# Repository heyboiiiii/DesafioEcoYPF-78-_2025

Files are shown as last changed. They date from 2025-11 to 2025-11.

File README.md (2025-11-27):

# PROYECTO YPF

## El proyecto original tenía como objetivo desarrollar la Computadora del Auto completa para el Desafío ECO YPF, incorporando diversos módulos de control y adquisición de datos para asistir al piloto. Dentro del conjunto de la Computadora, el Sistema de Control de Velocidad Crucero representaba solo una de las funcionalidades planificadas.
Sin embargo, durante el proceso surgieron diversos imprevistos que modificaron el alcance del proyecto. El viaje al autódromo, condiciones climáticas de tormenta que impidieron trabajar sobre el vehículo y, finalmente, un choque que dañó la placa principal del auto, imposibilitaron continuar con la integración de la computadora completa. Como consecuencia, se decidió enfocar el proyecto al desarrollo y funcionamiento del sistema de velocidad crucero utilizando una placa experimental.
Esta reestructuración permitió concentrarse en el diseño, programación y prueba del sistema decontrol de velocidad mediante ESP32, GPS y servomotor, con un sistema PID. Aunque no fue posible implementar la computadora entera del vehículo, el repositorio oficial del proyecto incluye el código completo de todos los módulos de la computadora, documentado y accesible.
En este informe se detalla el funcionamiento del sistema de velocidad crucero, su implementación, las pruebas realizadas y los resultados obtenidos en función del ensayo con la placa experimental.

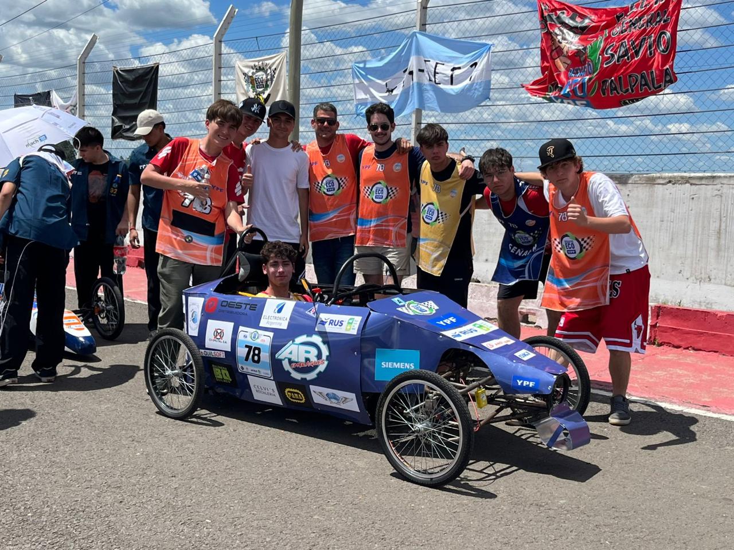
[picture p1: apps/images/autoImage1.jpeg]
FOTO 1 AUTO

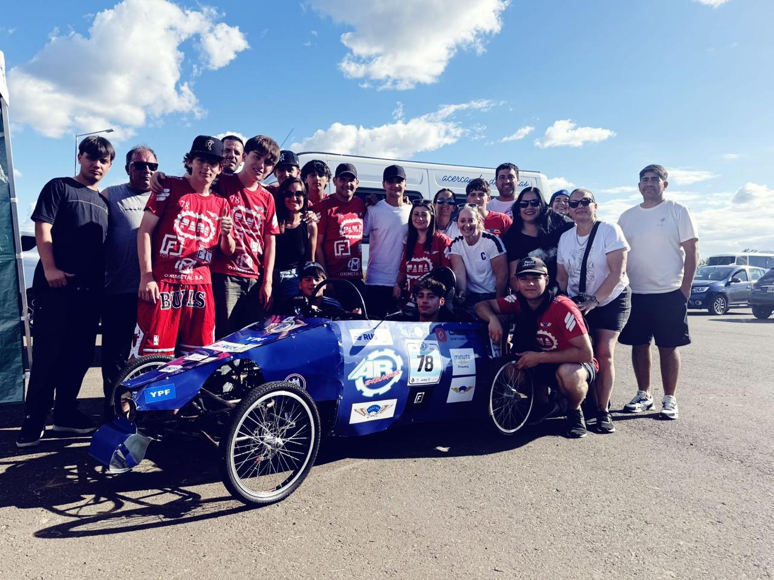
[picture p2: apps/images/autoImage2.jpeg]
FOTO 2 AUTO


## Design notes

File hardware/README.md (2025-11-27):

YPF KICAD DESIGNS

Esquemas y PCB de KICAD para la computadora del auto del "Desafío ECO YPF" y sus submódulos.

Proyecto *AUTO*:
    
    Computadora basada en un ESP32, una pantalla led ILI9844 montada en el volante(SPI), un acelerometro(MPU6050), modulo GPS(NEO6M) y un modulo LORA(XL1278).  

Proyecto *SHIELD_LORA*:
    
    Adaptación del módulo SMT1278 LoRa a un conector de 5 pines (header de 2.54 mm).

Proyecto *ACS_V_placa*:
    
    Aquí es donde los terminales de las baterías se conectan al sensor de corriente ACS712 (30A) y al divisor de voltaje.

    Esta placa se conectará a la placa del Proyecto AUTO mediante 3 cables.

Project_libraries: librerias de simbolos y huellas de los componentes creados para adaptar cada modulo a la placa.

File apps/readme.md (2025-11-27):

# Pagina web 

# Esta se encarga de mostrar al usuario toda la informacion que puede sensar la computadora del auto y la envia a traves de un modulo Lora SMT1278.

# La pagina web es alojada internamente en un servidor montado con LittleFS sobre el esp32 conectado en boxes como receptor.

# Para acceder a esta se debe primero conectar al Access Point generado por el esp32 con las credenciales cargadas y entrar por un navegador a la direccion IP del esp32 por el puerto 80.

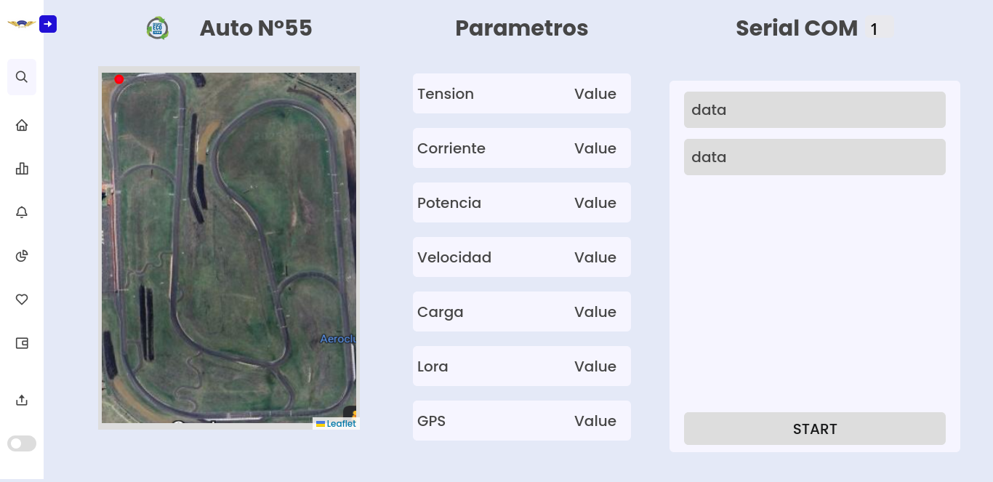
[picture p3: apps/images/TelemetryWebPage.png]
Muestra de la pagina web


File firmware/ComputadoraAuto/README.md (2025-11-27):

Firmware para la Computadora del Auto Desafio ECO YPF 2025

DESCRIPCIÓN DE LIBRERIAS

Libreria del Display (Manejo del display y fuentes de escritura):
    DISPLAY.c/.h & FONTS.c/.h

Libreria LoRa (Transmisor a Boxes)

Libreria GPS (NEO-6MV2)

Libreria Acelerómetro y Servo (MPU6050)

Info enviada por LoRa a Boxes:
latitud
longitud
voltaje
corriente
capacidad restante
velocidad

Display en auto:
    posee 2 windows: 
    1 - velocimetro
    2 - info: voltaje, corriente, capacidad bateria

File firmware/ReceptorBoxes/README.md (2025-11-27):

Receptor de telemetria en boxes(LORA).

1- Se recibira por el modulo SMT1278, la siguiente informacion del automovil:

    Tension y Corriente de baterias.
    Velocidad.
    Posicionamiento(Latitud & Longitud).
    Estado de pulsadores del volante.
    
2- Esta informacion es mostrada atraves de una pagina en un servidor interno montado por el esp32 con littleFS en una red local generada por el modulo WiFi del propio microcontrolador.

*Codigo de pagina web mas a detalle en directorio apps:

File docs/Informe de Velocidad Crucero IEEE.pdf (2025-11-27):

# Velocidad Crucero

Computadoras y Sistemas de Control, 6to 2da Avionica Comision A ´

Della Torre, Joaquin
joaquindellatorre@impatrq.com

Romero Domínguez, Braulio braulioromerodominguez@impatrq.com

Przybylski, Facundo
facundoprzybylski@impatrq.com

Reyes, Joaquin
joaquinreyes@impatrq.com

Pulido, Ignacio
ignaciopulido@impatrq.com

Abstract—Este proyecto desarrolla un Sistema de Control de Velocidad Crucero para el auto del Desafío ECO YPF, implementado con un microcontrolador ESP32 y un servomotor accionado mediante un sistema PID. La velocidad del vehículo se obtiene en tiempo real mediante un modulo GPS NEO-6MV2, cuyos datos ´ son procesados para regular la posicion del servo que opera sobre ´ el pedal que mueve el puno acelerador. Las pruebas realizadas ˜ con una placa experimental demostraron que el sistema mantiene una velocidad estable, responde adecuadamente a variaciones y se puede integrar de manera eficaz y segura al auto.

I. INTRODUCCION´
El proyecto original tenía como objetivo desarrollar la Computadora del Auto completa para el Desafío ECO YPF,
incorporando diversos modulos de control y adquisici ´ | on de ´
datos para asistir al piloto, enfocandose en este entorno de ´ taller en específico al sistema de Velocidad Crucero aunque dentro del conjunto de la Computadora, el Sistema de Control de Velocidad Crucero representaba solo una de las funcionalidades planificadas. Sin embargo, durante el proceso surgieron diversos imprevistos que modificaron el alcance del proyecto.
El viaje al autodromo, condiciones clim ´ | aticas de tormenta ´
que impidieron trabajar sobre el vehículo y, finalmente, un choque que danõ la placa principal del auto y en el que se ´
perdio la placa de volt ´ | ímetro y amperímetro que se encon-
traba junto a las baterías, imposibilitaron continuar con la integracion de la computadora completa. Como consecuencia, ´ se decidio enfocar el proyecto al desarrollo y funcionamiento ´ del sistema de Velocidad Crucero utilizando una placa ex-
perimental. Esta reestructuracion permiti ´ | o concentrarse en el ´
diseno, programaci ˜ | on y prueba del sistema de control de ´
velocidad con una ESP32, un modulo GPS y un servomotor, ´ mediante un sistema PID. Aunque no fue posible implementar la computadora entera del vehículo, el repositorio oficial del
proyecto incluye el codigo completo de todos los m ´ | odulos de ´
la computadora, documentado y accesible. En este informe se detalla el funcionamiento del sistema de velocidad crucero, su implementacion, las pruebas realizadas y los resultados ´ obtenidos en funcion del ensayo con la placa experimental. ´

II. DESCRIPCION´ FUNCIONAL

A. Diagrama en Bloques
A continuacion se observa el diagrama en bloques del ´ sistema.

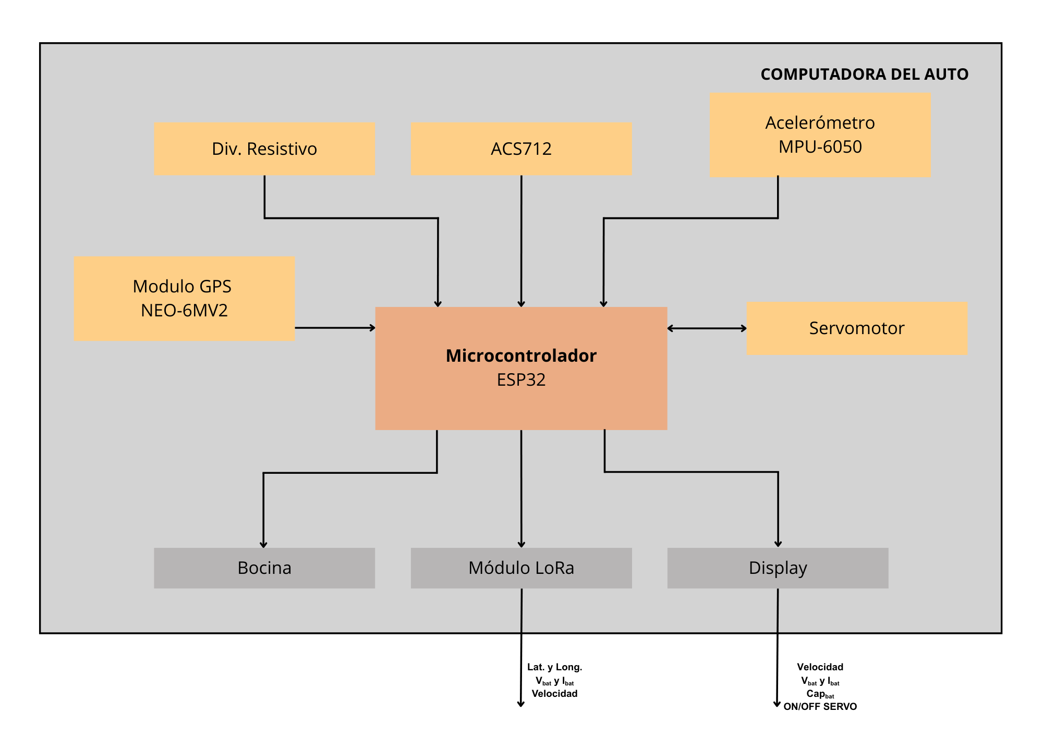
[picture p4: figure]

Fig. 1. Diagrama en bloques.

B. Diagrama de codigo ´

En la Figura 2 puede verse el diagrama de codigo de la ´ velocidad crucero.

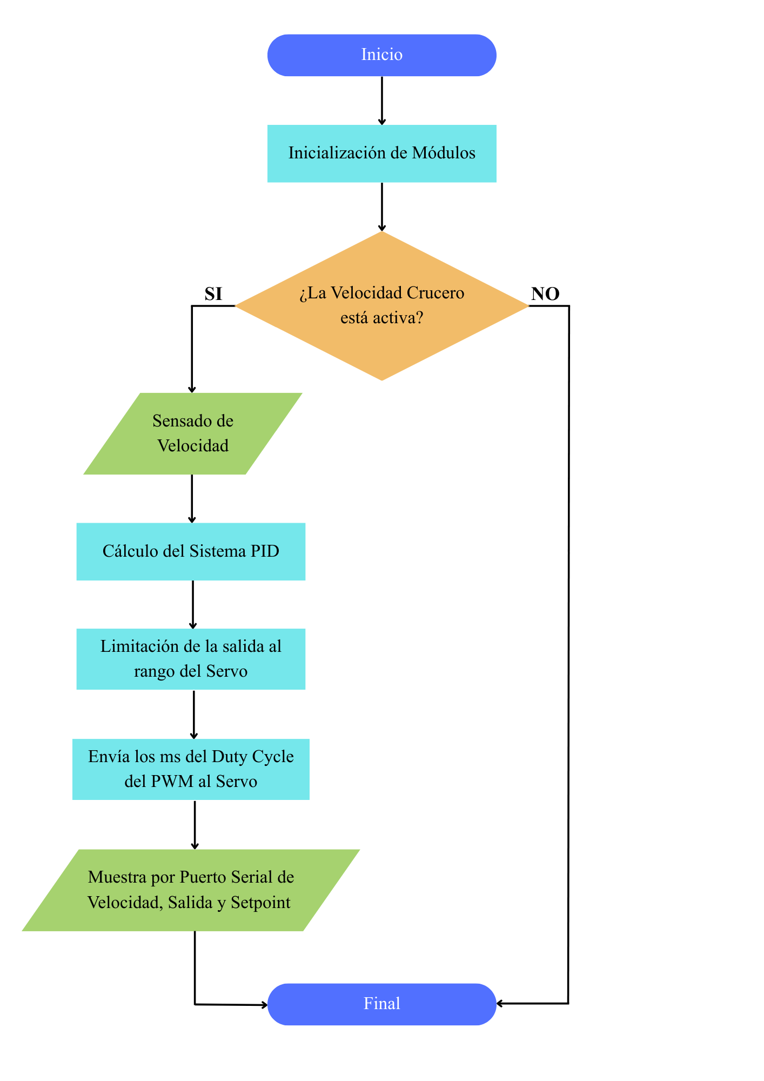
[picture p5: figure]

Fig. 2. Diagrama de codigo. ´

C. Descripcion de circuitos ´
- Modulo GPS: El M ´ | odulo GPS es el encargado de propor- ´
cionar en tiempo real la velocidad a la que se desplaza el auto. En este proyecto utilizamos el modelo NEO-6MV2,
el cual incluye internamente una funcion espec ´ | ífica para
calcular la velocidad a partir de los datos satelitales.
La informacion procesada por el m ´ | odulo es enviada a ´
la ESP32, que se encarga de interpretarla y utilizarla dentro del sistema de control para la implementacion de ´ la velocidad crucero.
- Microcontrolador ESP32: La ESP32 actua como el mi- ´ crocontrolador principal del sistema y es la encargada de procesar los datos de velocidad otorgados por el modulo ´ GPS. Sobre esta se implementa el algoritmo de control PID, que determina como debe actuar el sistema de ´ velocidad crucero. A partir de los calculos del PID, la ´ ESP32 genera la senal PWM necesaria para controlar el ˜ servomotor, ajustando su posicion seg ´ un la velocidad que ´ se desea mantener.
- Servomotor: El servomotor es el actuador principal del sistema de velocidad crucero. Recibe desde la ESP32
una senal PWM que indica el ˜ | angulo exacto al que debe ´
posicionarse. Segun este valor, el servo se mueve y tensa ´
un cable de acero, el cual esta conectado mec ´ | anicamente ´
al pedal del acelerador. Cuando el servomotor tira del cable, el pedal se acciona y, a su vez, este mueve el punõ acelerador, cumpliendo con el reglamento que no autoriza modificar el sistema desde el puno acelerador en adelante. ˜

III. ALCANCE LOGRADO
Logramos desarrollar un sistema de Velocidad Crucero funcional utilizando un microcontrolador ESP32 y un servomotor, cumpliendo el objetivo principal de implementar un sistema de control accesible, aplicable y coherente con el reglamento del Desafío ECO YPF. El sistema es capaz de leer e interpretar en tiempo real la velocidad del auto y ajustar automaticamente el accionamiento del servomotor para ´
mantener la velocidad deseada. En terminos de desempe ´ | no, ˜
su funcion central —accionar el servomotor para acelerar el ´ vehículo de manera estable mientras la Velocidad Crucero está activa— se ejecuta correctamente. Es importante destacar que el alcance final del proyecto, que estuvo influenciado por los diversos imprevistos ocurridos durante las etapas de trabajo, se vio limitado en cuanto a lo que se esperaba. Debido a las circunstancias imprevistas, el sistema debio desarrollarse y ´ probarse sobre una placa experimental independiente, lo que permitio continuar avanzando a pesar de las limitaciones del ´ entorno real.
Aun así, se observaron aspectos positivos, el sistema mostró una respuesta rapida del servomotor, fidelidad en la veloci- ´
dad que brinda el Modulo GPS, y una integraci ´ | on hard- ´
ware–software que demostro ser efectiva. Tambi ´ | en se com- ´
probo que el concepto puede incorporarse al auto sin requerir ´ modificaciones estructurales significativas.
Sin embargo, al tratarse de un ensayo inicial, se identificaron
algunas limitaciones. Sera necesario optimizar la ubicaci ´ | on de ´

la placa, el servomotor y el cableado para evitar interferencias
con el piloto durante la conduccion. Adem ´ | as, en esta prueba ´
la Velocidad Crucero permanecía activa mientras la ESP32 estuviera alimentada, lo cual puede resultar poco practico ´ o incluso riesgoso en situaciones donde el piloto necesite modificar la velocidad sin apagar todo el sistema. En resumen,
el sistema logro cumplir su objetivo funcional y demostr ´ | o un ´
desempeno correcto, aun cuando no se pudo integrar en la ˜ computadora completa del auto.

IV. CONCLUSIONES

El proyecto logro desarrollar un sistema de Velocidad ´ Crucero funcional e innovador para el Desafío ECO YPF, incorporando una característica completamente nueva para
el auto y manteniendo un diseno claro, seguro y ˜ | util para ´
el piloto. A lo largo del proceso adquirimos conocimientos importantes tanto en programacion de sistemas de control ´ como en la integracion f ´ ísica de hardware en un entorno real de competicion. Si bien el proyecto original fue reducido por ´
razones de fuerza mayor, esta version nos permiti ´ | o validar el ´
funcionamiento del sistema de velocidad crucero, confirmar su viabilidad y demostrar que puede integrarse al vehículo sin realizar modificaciones estructurales importantes.
Durante el trabajo tambien identificamos aspectos que pod ´ | ían
mejorarse en el futuro. Entre ellos, la necesidad de definir un soporte físico mas robusto para la placa, dado que los ´ soportes de la placa que iba al volante, impresos en 3D, se
danaron junto con la placa original. Ser ˜ | a necesario tambi ´ | en´
reorganizar el trazado de cables hacia el servomotor, evitando interferencias con los pedales o el espacio físico del piloto. Por otro lado, se podría optimizar el uso del sistema incorporando nuevamente un pulsador dedicado para activar y desactivar la Velocidad Crucero —pulsador que existía en la placa original—, ubicado directamente en el volante como exige el reglamento, ya que el piloto no puede retirar las manos durante la conduccion. ´
En conclusion, el proyecto alcanz ´ | o con ´ | exito su objetivo prin- ´
cipal: ofrecer un sistema funcional, novedoso y tecnicamente ´
solido, reconocido incluso por la Fundaci ´ | on YPF por su ´
caracter innovador. Adem ´ | as, nos permiti ´ | o aplicar de manera ´
concreta los contenidos trabajados en la materia, integrando teoría y practica en un desarrollo real. Las mejoras que ´ notamos en este primer ensayo serviran como base para ´ perfeccionar el sistema y optimizar su implementacion dentro ´ del auto del equipo.

ANEXOS

[1] Repositorio de Github del Proyecto [Online] https://github.com/heyboiiiii/DesafioEcoYPF-78- 2025
[2] Esquematico de la placa principal. ´

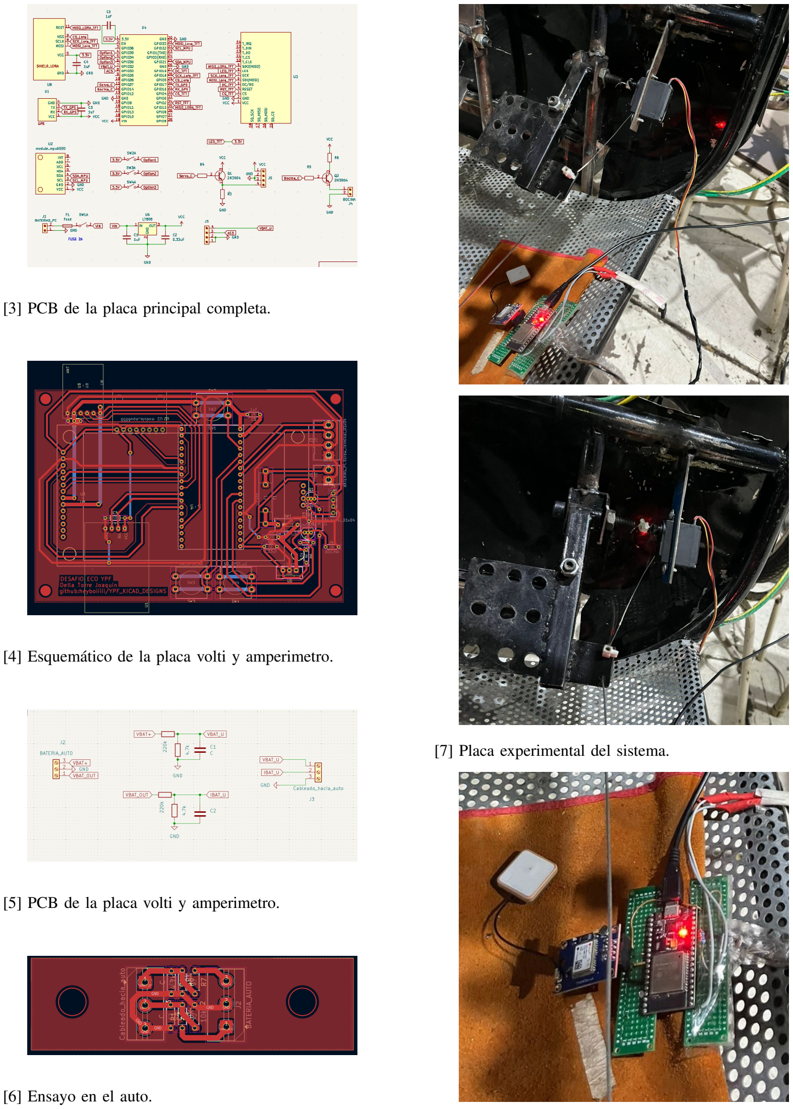
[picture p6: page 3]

[3] PCB de la placa principal completa.
[4] Esquematico de la placa volti y amperimetro. ´
[5] PCB de la placa volti y amperimetro.
[6] Ensayo en el auto.
[7] Placa experimental del sistema.

[8] Datasheet del Modulo GPS NEO-6MV2 [Online] ´ https://www.datasheethub.com/wp-content/uploads/2022/08/NEO6MV2-GPS-Module-Datasheet.pdf (https://www.datasheethub.com/wp-content/uploads/2022/08/NEO6MV2-GPS-Module-Datasheet.pdf)
[9] Videos de la prueba de la Velocidad Crucero [Online] https://drive.google.com/file/d/1-c 6ID6ugx3 mkt5zMJjeGTw7e tV-ty/view?usp=sharing (https://drive.google.com/file/d/1-c_6ID6ugx3_mkt5zMJjeGTw7e_tV-ty/view?usp=sharing) https://drive.google.com/file/d/18-ZetIGWumc2mcCzfIxSMozxGQ3JIxjF/view?usp=sharing (https://drive.google.com/file/d/18-ZetIGWumc2mcCzfIxSMozxGQ3JIxjF/view?usp=sharing)

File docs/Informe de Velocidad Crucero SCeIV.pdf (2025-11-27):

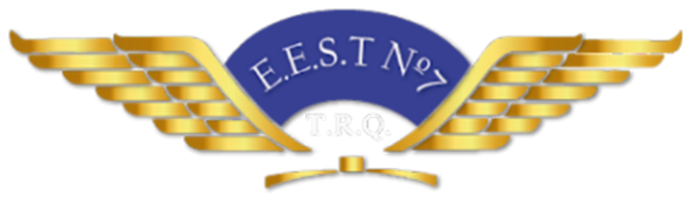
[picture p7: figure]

# VELOCIDAD CRUCERO

## Control de Velocidad Crucero mediante un Servomotor

Integrantes

Della Torre, Joaqu´ın
Pulido, Ignacio
Przybylski, Facundo
Reyes, Joaqu´ın
Romero Dom´ınguez, Braulio

Curso: 6to 2da Avionica ´

Materia: Sistemas de Control e Instrumentacion Virtual ´

Profesor: Maximiliano Testa

2025

Control de Velocidad Crucero mediante un Servomotor

## Abstract

Este proyecto desarrolla un Sistema de Control de Velocidad Crucero para el auto del Desaf´ıo ECO YPF, utilizando un servomotor accionado por un microcontrolador ESP32. El sistema fue desarrollado en el entorno Espressif ESP-IDF, programado en C++, e integra un control PID encargado de mantener estable la velocidad promedio del auto. La velocidad del veh´ıculo es medida en tiempo real mediante un modulo GPS NEO-6MV2, cuyos datos son procesados ´
por el PID para ajustar el servomotor que actua directamente sobre el pu ´ | no acelerador. Las ˜
pruebas realizadas demostraron que el sistema mantiene una velocidad constante de manera confiable, respondiendo adecuadamente a variaciones y ofreciendo una solucion eficaz, ´
segura y totalmente integrada al sistema de trasmision del veh ´ | ´ıculo.

## I. Descripcion funcional ´

### A. Diagrama de codigo ´


Figura 1: Diagrama de Flujo

### B. Descripcion del circuito ´

Modulo GPS: El M ´ | odulo GPS es el encargado de proporcionar en tiempo real la ve- ´
locidad a la que se desplaza el veh´ıculo. En este proyecto utilizamos el modelo NEO-
6MV2, el cual incluye internamente una funcion espec ´ | ´ıfica para calcular la velocidad
a partir de los datos satelitales. La informacion procesada por el m ´ | odulo es enviada a ´
la ESP32, que se encarga de interpretarla y utilizarla dentro del sistema de control para la implementacion de la velocidad crucero. ´
Microcontrolador ESP32: La ESP32 actua como el microcontrolador principal del sis- ´ tema y es la encargada de procesar los datos de velocidad otorgados por el modulo ´ GPS. Sobre esta se implementa el algoritmo de control PID, que determina como debe ´ actuar el sistema de velocidad crucero. A partir de los calculos del PID, la ESP32 ge- ´
nera la senal PWM necesaria para controlar el servomotor, ajustando su posici ˜ | on seg ´ | un´
la velocidad que se desea mantener.
Servomotor: El servomotor es el actuador principal del sistema de velocidad cruce-
ro. Recibe desde la ESP32 una senal PWM que indica el ˜ | angulo exacto al que debe ´
posicionarse. Segun este valor, el servo se mueve y tensa un cable de acero, el cual ´
esta conectado mec ´ | anicamente al pedal del acelerador. Cuando el servomotor tira del ´
cable, el pedal se acciona y, a su vez, este movimiento se transmite al puno acelera- ˜ dor, cumpliendo con el reglamento que no autoriza modificar el sistema desde el puno˜ acelerador en adelante.

## II. Alcance Logrado

Logramos desarrollar un sistema de Velocidad Crucero funcional utilizando un microcontrolador ESP32 y un servomotor, cumpliendo el objetivo principal de implementar un sistema de control accesible, aplicable y coherente con el reglamento. El sistema es capaz de leer e interpretar en tiempo real la velocidad del auto y ajustar automaticamente el accionamiento ´
del servomotor para mantener la velocidad deseada. En terminos de desempe ´ | no, su funci ˜ | on´
central que es accionar el servomotor para acelerar el auto de manera estable mientras la Velocidad Crucero esta activa se ejecuta correctamente. En cuanto a los aspectos positivos, el ´
sistema demostro r ´ apida respuesta del servomotor y una integraci ´ | on efectiva entre hardware ´
y software. Ademas, se comprob ´ | o que la idea puede incorporarse sin generar modificaciones ´
estructurales importantes en el auto. Sin embargo, tambien identificamos algunas limitacio- ´ nes. Al tratarse de un ensayo inicial, es necesario optimizar la ubicacion de la placa y del ´ cableado que alimenta el servomotor, para evitar interferencias con el piloto durante la con-
duccion. Por otro lado, en esta prueba la Velocidad Crucero permanec ´ | ´ıa activa mientras la
ESP32 estuviera alimentada, lo cual puede resultar poco practico o incluso peligroso en si- ´ tuaciones donde el piloto necesite modificar la velocidad o frenar sin apagar todo el sistema.
En resumen, el sistema logro cumplir su objetivo funcional demostrando un desempe ´ | no co- ˜
rrecto, aunque aun requiere mejoras estructurales y de interfaz para garantizar un uso seguro ´ y eficiente dentro del auto.

## III. Conclusiones

El proyecto consiguio cumplir con el objetivo de desarrollar un sistema innovador para el ´ Desaf´ıo ECO YPF, incorporando una funcion completamente nueva para el auto y, al mismo ´
tiempo, manteniendo un diseno claro y ˜ | util para el piloto. A lo largo del proceso adquirimos ´
conocimientos valiosos tanto en la programacion y aplicaci ´ | on de un sistema de control como ´
en el diseno f ˜ | ´ısico y la integracion de hardware en un entorno real. En el proceso identifica- ´
mos tambien aspectos que pueden mejorarse. Entre ellos, la necesidad de definir un soporte ´ f´ısico fijo para la placa —lo que se esperaba es que fuera el volante— y un trazado de cables hacia el servomotor que no interfiera con los pedales ni con el espacio f´ısico del piloto.
Ademas, se podr ´ | ´ıa optimizar el sistema incorporando un pulsador para activar o desactivar
la Velocidad Crucero, ubicandolo directamente en el volante tal como exige el reglamento ´ —porque el piloto no puede sacar las manos del volante—. En conclusion, el proyecto al- ´ canzo su meta principal: brindar un sistema funcional, novedoso y reconocido por la Funda- ´
cion YPF como una propuesta innovadora. A la vez, nos permiti ´ | o aplicar de manera pr ´ | actica ´
los contenidos trabajados en la materia, integrando la teor´ıa vista en una situacion real. Las ´ mejoras observadas en este primer ensayo serviran para perfeccionar el sistema y optimizar ´ al maximo el mismo. ´

## IV. Anexos

1. Repositorio de Github del Proyecto [Online]

github.com/heyboiiiii/DesafioEcoYPF-78-2025

2. Ensayo de la Velocidad Crucero

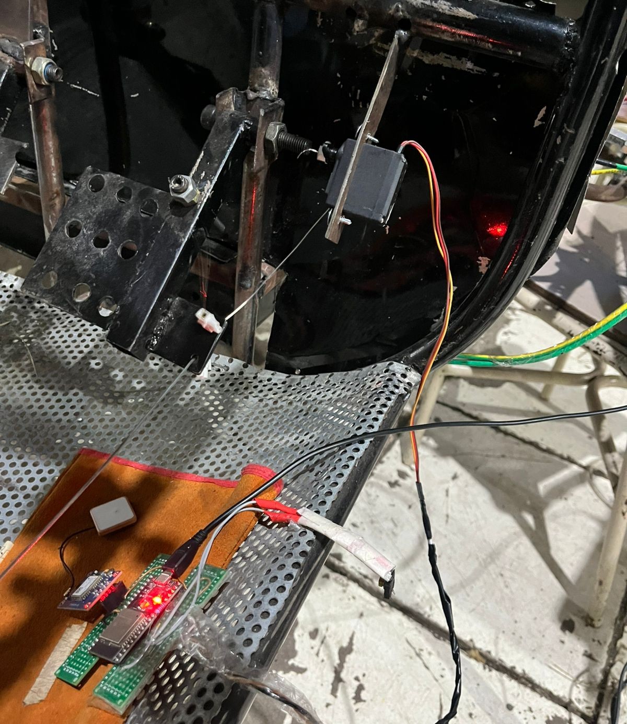
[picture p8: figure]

Figura 2: Sistema en el Auto

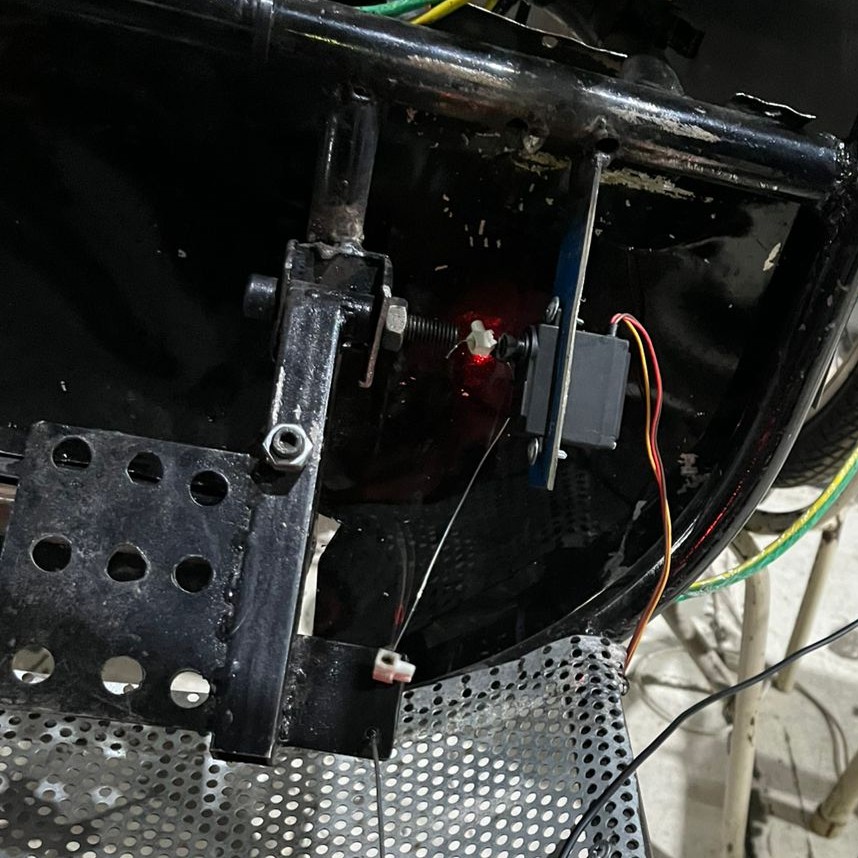
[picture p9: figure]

Figura 3: Servomotor accionado

3. Placa del Sistema

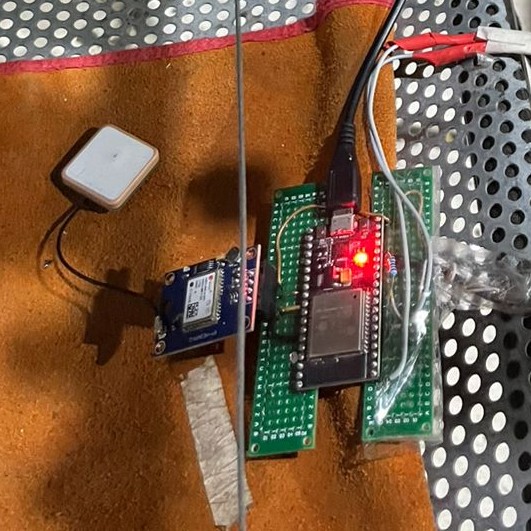
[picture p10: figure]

Figura 4: ESP32 y Modulo GPS ´

4. Puno acelerador del Auto ˜

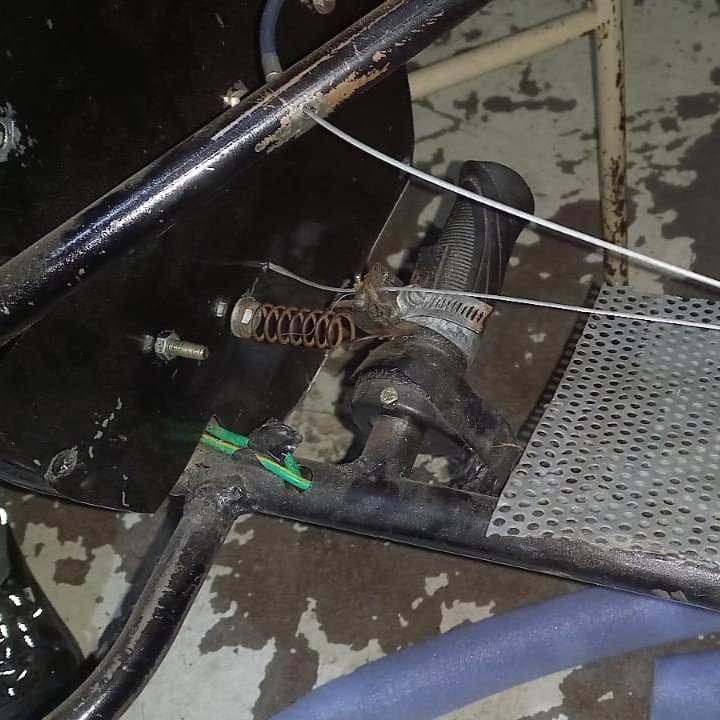
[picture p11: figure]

Figura 5: Puno siendo accionado por el servo ˜

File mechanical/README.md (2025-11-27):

1- Chasis:
    
    Planos utilizados para el desarrollo del chasis del auto.

2- Volante:

    Planos de la pieza que soporta la placa electronica de la computadora del auto al volante del mismo.

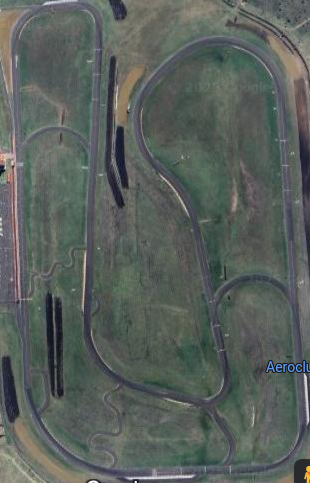
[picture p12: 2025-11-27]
apps/WebPageTelemetry/autodromo.png

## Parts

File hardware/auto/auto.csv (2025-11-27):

Id | Identificador | Huella | Cantidad | Identificación | Suministrador y ref
1 | U8 | SHIELD XL1278 | 1 | ~
2 | F1 | Fuseholder_Clip-5x20mm_Littelfuse_445-030_Inline_P20.50x5.20mm_D1.30mm_Horizontal | 1 | Fuse
3 | ,,,,,,, |  | 8
4 | C5,C4,C3,C1 | R_Axial_DIN0204_L3.6mm_D1.6mm_P5.08mm_Horizontal | 4 | 1uF
5 | U3 | tft_3.5_display | 1 | ~
6 | Q1,Q2 | TO-92_Inline | 2 | 2N3904
7 | R5,R3,R6 | R_Axial_DIN0204_L3.6mm_D1.6mm_P5.08mm_Horizontal | 3 | 10k
8 | U4 | esp32 | 1 | ~
9 | J3 | PinHeader_1x03_P2.54mm_Vertical | 1 | servo
10 | SW2 | SW_PUSH-12mm_Wuerth-430476085716 | 1 | SW1
11 | U2 | module_MPU6050 | 1 | module_mpu6050
12 | U1 | GY-NEO6MV2 | 1 | ~
13 | SW4,SW3 | SW_PUSH-12mm_Wuerth-430476085716 | 2 | SW_DPST_x2
14 | J1 | TerminalBlock_MaiXu_MX126-5.0-02P_1x02_P5.00mm | 1 | BATERIAS_PC
15 | R4 | R_Axial_DIN0207_L6.3mm_D2.5mm_P10.16mm_Horizontal | 1 | 10k
16 | J2 | TerminalBlock_MaiXu_MX126-5.0-03P_1x03_P5.00mm | 1 | Cableado_hacia_auto
17 | J4 | PinHeader_1x02_P2.54mm_Vertical | 1 | BOCINA
18 | C2 | R_Axial_DIN0204_L3.6mm_D1.6mm_P5.08mm_Horizontal | 1 | 0.33uF
19 | U6 | TO-220-3_Vertical | 1 | L7805
20 | SW1 | SW_DIP_SPSTx01_Slide_9.78x4.72mm_W7.62mm_P2.54mm | 1 | SW_DPST_x2

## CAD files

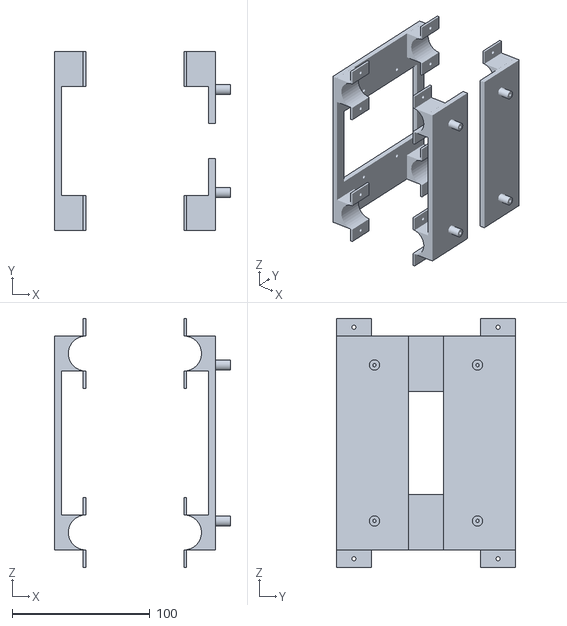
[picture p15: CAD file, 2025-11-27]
mechanical/volante/soportevolante.stl
127.7 x 130.0 x 180.5

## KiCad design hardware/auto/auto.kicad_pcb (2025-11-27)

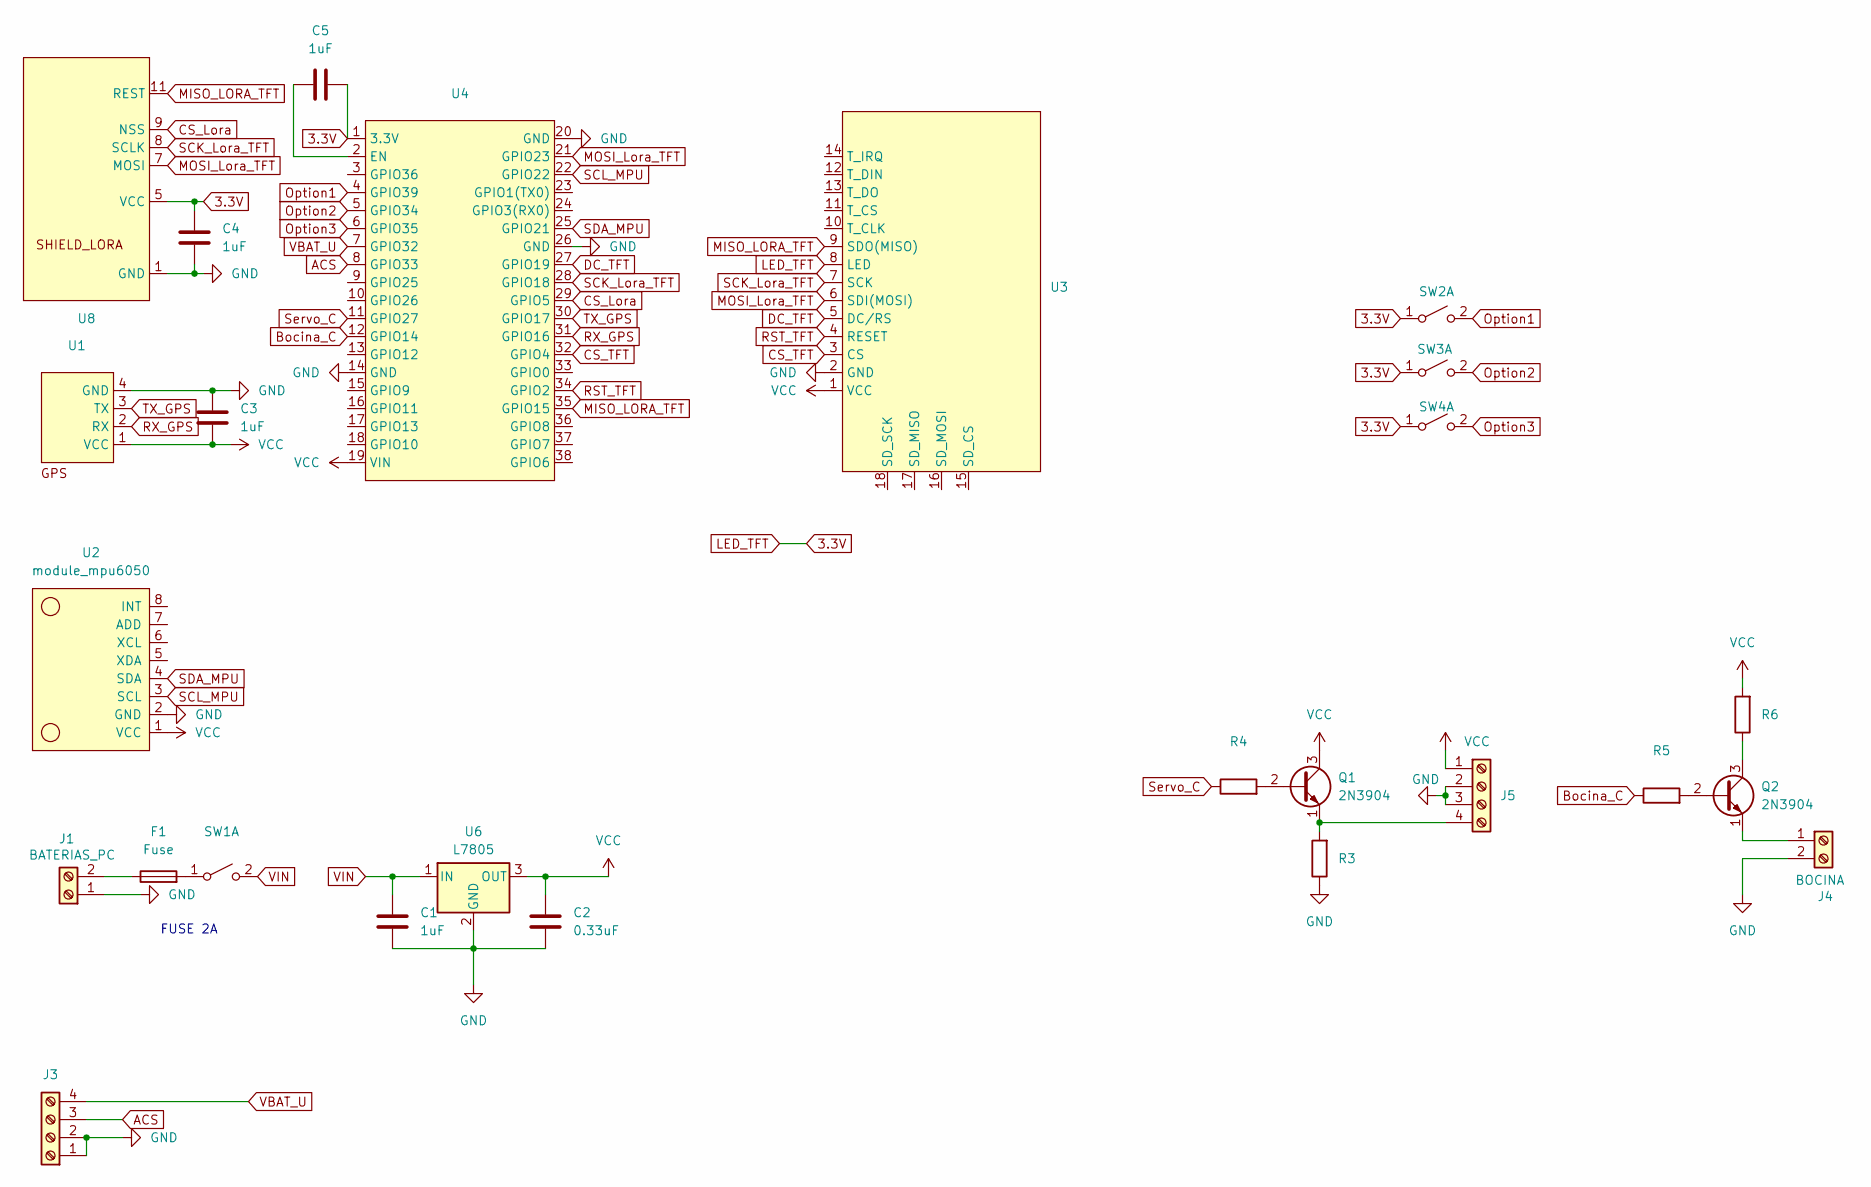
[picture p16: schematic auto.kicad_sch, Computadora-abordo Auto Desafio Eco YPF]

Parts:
C1, C4, C5: 1uF; R_Axial_DIN0204_L3.6mm_D1.6mm_P5.08mm_Horizontal
C2: 0.33uF; R_Axial_DIN0204_L3.6mm_D1.6mm_P5.08mm_Horizontal
C3: 1uF; R_Axial_DIN0204_L3.6mm_D1.6mm_P7.62mm_Horizontal
F1: Fuse; Fuseholder_Clip-5x20mm_Littelfuse_445-030_Inline_P20.50x5.2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
J1: BATERIAS_PC; Molex_KK-396_5273-02A_1x02_P3.96mm_Vertical
J3: Screw_Terminal_01x04; Molex_KK-396_5273-04A_1x04_P3.96mm_Vertical
J4: BOCINA; R_Axial_DIN0204_L3.6mm_D1.6mm_P5.08mm_Horizontal
J5: Screw_Terminal_01x04; PinSocket_1x04_P2.54mm_Vertical
Q1, Q2: 2N3904; TO-92_Inline
R3, R5, R6: 10k; R_Axial_DIN0204_L3.6mm_D1.6mm_P5.08mm_Horizontal
R4: 10k; R_Axial_DIN0207_L6.3mm_D2.5mm_P10.16mm_Horizontal
SW1: SW_DPST_x2; SW_DIP_SPSTx01_Slide_9.78x4.72mm_W7.62mm_P2.54mm
SW2: SW1; SW_PUSH-12mm_Wuerth-430476085716
SW3, SW4: SW_DPST_x2; SW_PUSH-12mm_Wuerth-430476085716
U1: GY-NEO6MV2
U2: module_mpu6050; module_MPU6050
U3: tft_3.5_display
U4: esp32
U6: L7805; TO-220-3_Vertical
U8: SHIELD XL1278

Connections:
3.3V: C4.1, C5.2, SW2.1 (A), SW3.1 (A), SW4.1 (A), U3.8 (LED), U4.1 (3.3V), U8.5 (VCC)
ACS: J3.3, U4.8 (GPIO33)
Bocina_C: R5.1, U4.12 (GPIO14)
CS_Lora: U4.29 (GPIO5), U8.9 (NSS)
CS_TFT: U3.3 (CS), U4.32 (GPIO4)
DC_TFT: U3.5 (DC/RS), U4.27 (GPIO19)
GND: C1.2, C2.2, C3.1, C4.2, J1.1, J3.1, J3.2, J4.2, J5.2, J5.3, R3.1, U1.4 (GND), U2.2 (GND), U3.2 (GND), U4.14 (GND), U4.20 (GND), U4.26 (GND), U6.2 (GND), U8.1 (GND)
MISO_LORA_TFT: U3.9 (SDO(MISO)), U4.35 (GPIO15), U8.11 (REST)
MOSI_Lora_TFT: U3.6 (SDI(MOSI)), U4.21 (GPIO23), U8.7 (MOSI)
unnamed: F1.1, J1.2
unnamed: J4.1, Q2.1 (E)
unnamed: J5.4, Q1.1 (E), R3.2
unnamed: Q1.2 (B), R4.2
unnamed: Q2.2 (B), R5.2
unnamed: Q2.3 (C), R6.1
unnamed: F1.2, SW1.1 (A)
unnamed: C5.1, U4.2 (EN)
Option1: SW2.2 (B), U4.4 (GPIO39)
Option2: SW3.2 (B), U4.5 (GPIO34)
Option3: SW4.2 (B), U4.6 (GPIO35)
RST_TFT: U3.4 (RESET), U4.34 (GPIO2)
RX_GPS: U1.2 (RX), U4.31 (GPIO16)
SCK_Lora_TFT: U3.7 (SCK), U4.28 (GPIO18), U8.8 (SCLK)
SCL_MPU: U2.3 (SCL), U4.22 (GPIO22)
SDA_MPU: U2.4 (SDA), U4.25 (GPIO21)
Servo_C: R4.1, U4.11 (GPIO27)
TX_GPS: U1.3 (TX), U4.30 (GPIO17)
VBAT_U: J3.4, U4.7 (GPIO32)
VCC: C2.1, C3.2, J5.1, Q1.3 (C), R6.2, U1.1 (VCC), U2.1 (VCC), U3.1 (VCC), U4.19 (VIN), U6.3 (OUT)
VIN: C1.1, SW1.2 (B), U6.1 (IN)

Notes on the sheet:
FUSE 2A

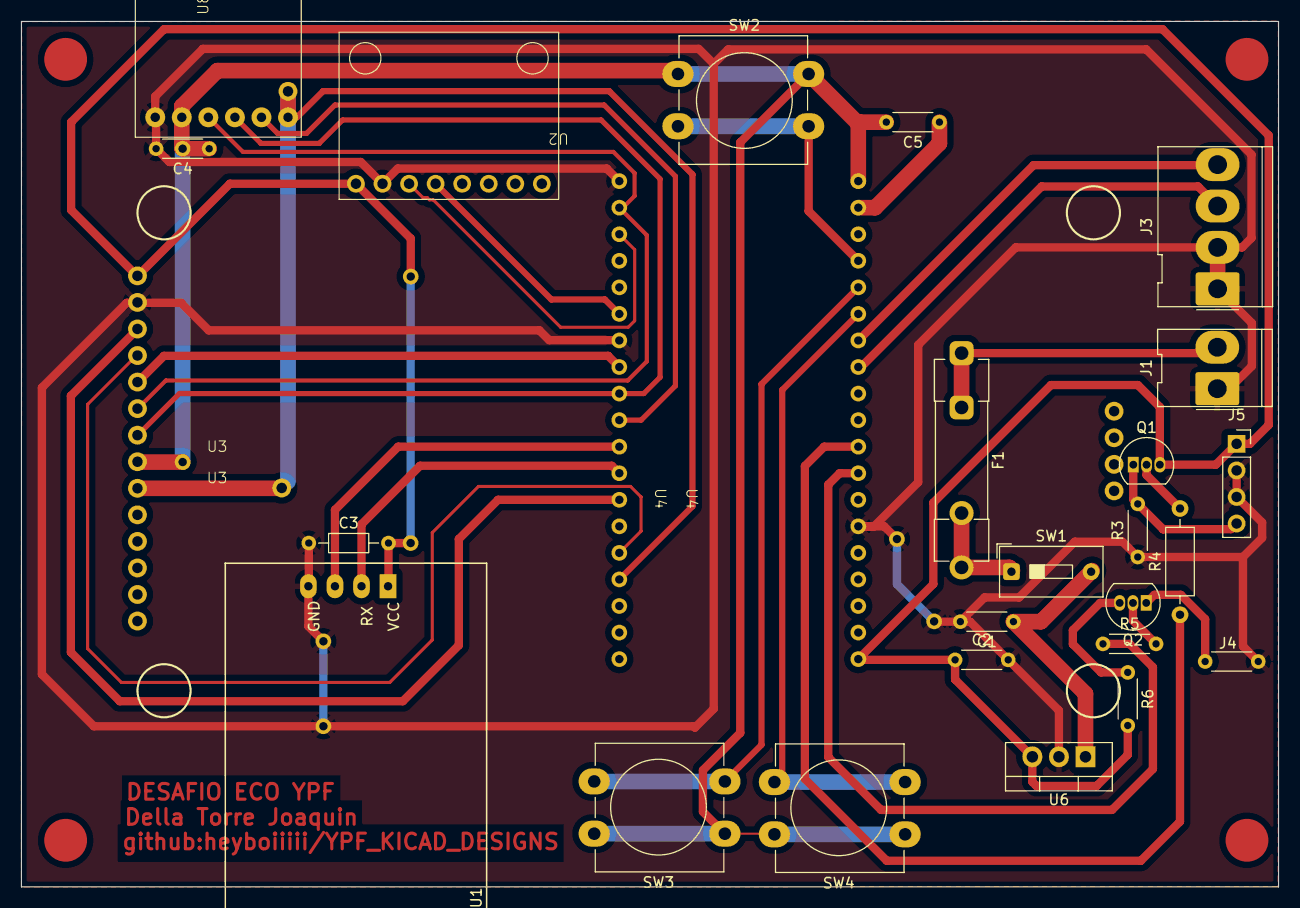
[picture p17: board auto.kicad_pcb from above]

Board: 2 copper layers, 120.2 x 82.8 mm, 26 parts (0 on the bottom side), 30 nets.

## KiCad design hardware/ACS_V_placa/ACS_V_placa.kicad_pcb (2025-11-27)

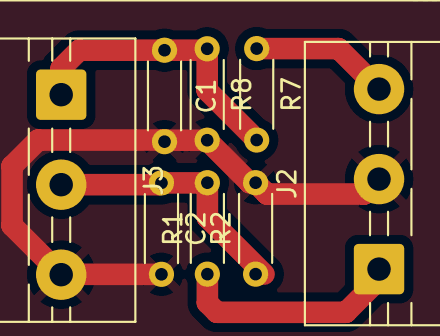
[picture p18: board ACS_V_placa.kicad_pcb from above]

Board: 2 copper layers, 8 parts (0 on the bottom side), 5 nets.

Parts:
C1, C2: C; R_Axial_DIN0204_L3.6mm_D1.6mm_P5.08mm_Horizontal
J2: BATERIA_AUTO; TerminalBlock_MaiXu_MX126-5.0-03P_1x03_P5.00mm
J3: Cableado_hacia_auto; TerminalBlock_MaiXu_MX126-5.0-03P_1x03_P5.00mm
R1: 10K; R_Axial_DIN0204_L3.6mm_D1.6mm_P5.08mm_Horizontal
R2: 10k; R_Axial_DIN0204_L3.6mm_D1.6mm_P5.08mm_Horizontal
R7: 220k; R_Axial_DIN0204_L3.6mm_D1.6mm_P5.08mm_Horizontal
R8: 4.7k; R_Axial_DIN0204_L3.6mm_D1.6mm_P5.08mm_Horizontal

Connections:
GND: C1.2, C2.2, J2.2, J3.3, R2.2, R8.2
IBAT_U: C2.1, J3.2, R1.2, R2.1
VBAT+: J2.3, R7.1
VBAT_OUT: J2.1, R1.1
VBAT_U: C1.1, J3.1, R7.2, R8.1

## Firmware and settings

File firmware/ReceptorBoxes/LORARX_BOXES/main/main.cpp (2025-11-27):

#include <stdio.h>
#include <string.h>
#include "freertos/FreeRTOS.h"
#include "freertos/task.h"
#include "esp_log.h"
#include "esp_system.h"
#include "esp_littlefs.h"
#include "nvs_flash.h"
#include "esp_netif.h"
#include "esp_event.h"
#include "esp_wifi.h"
#include "esp_http_server.h"

// LoRa includes
#include "driver/spi_master.h"
#include "src/LoRa.h"

// LoRa pins
#define LORA_MISO 22
#define LORA_MOSI 23
#define LORA_SCK  15
#define LORA_SS   4
#define LORA_DIO0 21
#define LORA_RST  3

static const char *TAG = "MAIN";

// LoRa parameters
float tension = 0.0;
float corriente = 0.0;

// LittleFS configuration
static const esp_vfs_littlefs_conf_t littlefs_conf = {
    .base_path = "/littlefs",
    .partition_label = "littlefs",
    .format_if_mount_failed = true,
    .dont_mount = false
};

// ==================== HTTP HANDLER ====================
esp_err_t data_get_handler(httpd_req_t *req) {
    char buf[128];
    snprintf(buf, sizeof(buf), "{\"voltage\":%.2f,\"current\":%.2f}", tension, corriente);
    httpd_resp_set_type(req, "application/json");
    return httpd_resp_send(req, buf, strlen(buf));
}

httpd_uri_t data_uri = {
    .uri       = "/data",
    .method    = HTTP_GET,
    .handler   = data_get_handler,
    .user_ctx  = NULL
};

// Simple file handler for static files
esp_err_t file_get_handler(httpd_req_t *req) {
    char filepath[1000];
    snprintf(filepath, sizeof(filepath), "/littlefs/%s", req->uri);

    FILE *f = fopen("index.html", "r");
    if (!f) {
        httpd_resp_send_404(req);
        return ESP_FAIL;
    }

    char buf[512];
    size_t n;
    while ((n = fread(buf, 1, sizeof(buf), f)) > 0) {
        httpd_resp_send_chunk(req, buf, n);
    }
    fclose(f);
    httpd_resp_send_chunk(req, NULL, 0); // end response
    return ESP_OK;
}

httpd_uri_t file_uri = {
    .uri       = "/*",
    .method    = HTTP_GET,
    .handler   = file_get_handler,
    .user_ctx  = NULL
};

// ==================== MAIN TASK ====================
extern "C" void app_main(void)
{
    // Initialize NVS
    esp_err_t ret = nvs_flash_init();
    if (ret == ESP_ERR_NVS_NO_FREE_PAGES || ret == ESP_ERR_NVS_NEW_VERSION_FOUND) {
        ESP_ERROR_CHECK(nvs_flash_erase());
        ret = nvs_flash_init();
    }
    ESP_ERROR_CHECK(ret);

    // Initialize TCP/IP stack
    ESP_ERROR_CHECK(esp_netif_init());

    // Create default event loop
    ESP_ERROR_CHECK(esp_event_loop_create_default());

    // Initialize default WiFi AP network interface
    esp_netif_create_default_wifi_ap();

    // WiFi initialization
    wifi_init_config_t cfg = WIFI_INIT_CONFIG_DEFAULT();
    ESP_ERROR_CHECK(esp_wifi_init(&cfg));

    // Set WiFi mode to AP
    ESP_ERROR_CHECK(esp_wifi_set_mode(WIFI_MODE_AP));

    // Configure AP
    wifi_config_t ap_config = {};
    strcpy((char*)ap_config.ap.ssid, "Monitoreo");
    strcpy((char*)ap_config.ap.password, "19791979");
    ap_config.ap.ssid_len = strlen("Monitoreo");
    ap_config.ap.max_connection = 4;
    ap_config.ap.authmode = WIFI_AUTH_WPA_WPA2_PSK;
    ESP_ERROR_CHECK(esp_wifi_set_config(WIFI_IF_AP, &ap_config));
    ESP_ERROR_CHECK(esp_wifi_start());
    ESP_LOGI(TAG, "Access Point started");

    // Initialize LittleFS
    ESP_ERROR_CHECK(esp_vfs_littlefs_register(&littlefs_conf));
    ESP_LOGI(TAG, "LittleFS mounted at %s", littlefs_conf.base_path);

    // Start HTTP server
    httpd_config_t server_config = HTTPD_DEFAULT_CONFIG();
    httpd_handle_t server = nullptr;
    ESP_ERROR_CHECK(httpd_start(&server, &server_config));
    httpd_register_uri_handler(server, &data_uri);
    httpd_register_uri_handler(server, &file_uri);
    ESP_LOGI(TAG, "HTTP server started");

    // Initialize LoRa (example only)
    /*
    SPI.begin(LORA_SCK, LORA_MISO, LORA_MOSI, LORA_SS);
    LoRa.setPins(LORA_SS, LORA_RST, LORA_DIO0);
    if (!LoRa.begin(433E6)) {
        ESP_LOGE(TAG, "LoRa init failed");
        while (1);
    }
    ESP_LOGI(TAG, "LoRa Receiver ready");
    */

    // Application main loop
    while (1) {
        vTaskDelay(pdMS_TO_TICKS(1000));
    }
}

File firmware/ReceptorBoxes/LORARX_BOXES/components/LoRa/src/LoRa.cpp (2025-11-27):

// Copyright (c) Sandeep Mistry. All rights reserved.
// Licensed under the MIT license. See LICENSE file in the project root for full license information.

#include <src/LoRa.h>

// registers
#define REG_FIFO                 0x00
#define REG_OP_MODE              0x01
#define REG_FRF_MSB              0x06
#define REG_FRF_MID              0x07
#define REG_FRF_LSB              0x08
#define REG_PA_CONFIG            0x09
#define REG_OCP                  0x0b
#define REG_LNA                  0x0c
#define REG_FIFO_ADDR_PTR        0x0d
#define REG_FIFO_TX_BASE_ADDR    0x0e
#define REG_FIFO_RX_BASE_ADDR    0x0f
#define REG_FIFO_RX_CURRENT_ADDR 0x10
#define REG_IRQ_FLAGS            0x12
#define REG_RX_NB_BYTES          0x13
#define REG_PKT_SNR_VALUE        0x19
#define REG_PKT_RSSI_VALUE       0x1a
#define REG_RSSI_VALUE           0x1b
#define REG_MODEM_CONFIG_1       0x1d
#define REG_MODEM_CONFIG_2       0x1e
#define REG_PREAMBLE_MSB         0x20
#define REG_PREAMBLE_LSB         0x21
#define REG_PAYLOAD_LENGTH       0x22
#define REG_MODEM_CONFIG_3       0x26
#define REG_FREQ_ERROR_MSB       0x28
#define REG_FREQ_ERROR_MID       0x29
#define REG_FREQ_ERROR_LSB       0x2a
#define REG_RSSI_WIDEBAND        0x2c
#define REG_DETECTION_OPTIMIZE   0x31
#define REG_INVERTIQ             0x33
#define REG_DETECTION_THRESHOLD  0x37
#define REG_SYNC_WORD            0x39
#define REG_INVERTIQ2            0x3b
#define REG_DIO_MAPPING_1        0x40
#define REG_VERSION              0x42
#define REG_PA_DAC               0x4d

// modes
#define MODE_LONG_RANGE_MODE     0x80
#define MODE_SLEEP               0x00
#define MODE_STDBY               0x01
#define MODE_TX                  0x03
#define MODE_RX_CONTINUOUS       0x05
#define MODE_RX_SINGLE           0x06

// PA config
#define PA_BOOST                 0x80

// IRQ masks
#define IRQ_TX_DONE_MASK           0x08
#define IRQ_PAYLOAD_CRC_ERROR_MASK 0x20
#define IRQ_RX_DONE_MASK           0x40

#define RF_MID_BAND_THRESHOLD    525E6
#define RSSI_OFFSET_HF_PORT      157
#define RSSI_OFFSET_LF_PORT      164

#define MAX_PKT_LENGTH           255

#if (ESP8266 || ESP32)
    #define ISR_PREFIX ICACHE_RAM_ATTR
#else
    #define ISR_PREFIX
#endif

LoRaClass::LoRaClass() :
  _spiSettings(LORA_DEFAULT_SPI_FREQUENCY, MSBFIRST, SPI_MODE0),
  _spi(&LORA_DEFAULT_SPI),
  _ss(LORA_DEFAULT_SS_PIN), _reset(LORA_DEFAULT_RESET_PIN), _dio0(LORA_DEFAULT_DIO0_PIN),
  _frequency(0),
  _packetIndex(0),
  _implicitHeaderMode(0),
  _onReceive(NULL),
  _onTxDone(NULL)
{
  // overide Stream timeout value
  setTimeout(0);
}

int LoRaClass::begin(long frequency)
{
#if defined(ARDUINO_SAMD_MKRWAN1300) || defined(ARDUINO_SAMD_MKRWAN1310)
  pinMode(LORA_IRQ_DUMB, OUTPUT);
  digitalWrite(LORA_IRQ_DUMB, LOW);

  // Hardware reset
  pinMode(LORA_BOOT0, OUTPUT);
  digitalWrite(LORA_BOOT0, LOW);

  pinMode(LORA_RESET, OUTPUT);
  digitalWrite(LORA_RESET, HIGH);
  delay(200);
  digitalWrite(LORA_RESET, LOW);
  delay(200);
  digitalWrite(LORA_RESET, HIGH);
  delay(50);
#endif

  // setup pins
  pinMode(_ss, OUTPUT);
  // set SS high
  digitalWrite(_ss, HIGH);

  if (_reset != -1) {
    pinMode(_reset, OUTPUT);

    // perform reset
    digitalWrite(_reset, LOW);
    delay(10);
    digitalWrite(_reset, HIGH);
    delay(10);
  }

  // start SPI
  _spi->begin();

  // check version
  uint8_t version = readRegister(REG_VERSION);
  if (version != 0x12) {
    return 0;
  }

  // put in sleep mode
  sleep();

  // set frequency
  setFrequency(frequency);

  // set base addresses
  writeRegister(REG_FIFO_TX_BASE_ADDR, 0);
  writeRegister(REG_FIFO_RX_BASE_ADDR, 0);

  // set LNA boost
  writeRegister(REG_LNA, readRegister(REG_LNA) | 0x03);

  // set auto AGC
  writeRegister(REG_MODEM_CONFIG_3, 0x04);

  // set output power to 17 dBm
  setTxPower(17);

  // put in standby mode
  idle();

  return 1;
}

void LoRaClass::end()
{
  // put in sleep mode
  sleep();

  // stop SPI
  _spi->end();
}

int LoRaClass::beginPacket(int implicitHeader)
{
  if (isTransmitting()) {
    return 0;
  }

  // put in standby mode
  idle();

  if (implicitHeader) {
    implicitHeaderMode();
  } else {
    explicitHeaderMode();
  }

  // reset FIFO address and paload length
  writeRegister(REG_FIFO_ADDR_PTR, 0);
  writeRegister(REG_PAYLOAD_LENGTH, 0);

  return 1;
}

int LoRaClass::endPacket(bool async)
{
  
  if ((async) && (_onTxDone))
      writeRegister(REG_DIO_MAPPING_1, 0x40); // DIO0 => TXDONE

  // put in TX mode
  writeRegister(REG_OP_MODE, MODE_LONG_RANGE_MODE | MODE_TX);

  if (!async) {
    // wait for TX done
    while ((readRegister(REG_IRQ_FLAGS) & IRQ_TX_DONE_MASK) == 0) {
      yield();
    }
    // clear IRQ's
    writeRegister(REG_IRQ_FLAGS, IRQ_TX_DONE_MASK);
  }

  return 1;
}

bool LoRaClass::isTransmitting()
{
  if ((readRegister(REG_OP_MODE) & MODE_TX) == MODE_TX) {
    return true;
  }

  if (readRegister(REG_IRQ_FLAGS) & IRQ_TX_DONE_MASK) {
    // clear IRQ's
    writeRegister(REG_IRQ_FLAGS, IRQ_TX_DONE_MASK);
  }

  return false;
}

int LoRaClass::parsePacket(int size)
{
  int packetLength = 0;
  int irqFlags = readRegister(REG_IRQ_FLAGS);

  if (size > 0) {
    implicitHeaderMode();

    writeRegister(REG_PAYLOAD_LENGTH, size & 0xff);
  } else {
    explicitHeaderMode();
  }

  // clear IRQ's
  writeRegister(REG_IRQ_FLAGS, irqFlags);

  if ((irqFlags & IRQ_RX_DONE_MASK) && (irqFlags & IRQ_PAYLOAD_CRC_ERROR_MASK) == 0) {
    // received a packet
    _packetIndex = 0;

    // read packet length
    if (_implicitHeaderMode) {
      packetLength = readRegister(REG_PAYLOAD_LENGTH);
    } else {
      packetLength = readRegister(REG_RX_NB_BYTES);
    }

    // set FIFO address to current RX address
    writeRegister(REG_FIFO_ADDR_PTR, readRegister(REG_FIFO_RX_CURRENT_ADDR));

    // put in standby mode
    idle();
  } else if (readRegister(REG_OP_MODE) != (MODE_LONG_RANGE_MODE | MODE_RX_SINGLE)) {
    // not currently in RX mode

    // reset FIFO address
    writeRegister(REG_FIFO_ADDR_PTR, 0);

    // put in single RX mode
    writeRegister(REG_OP_MODE, MODE_LONG_RANGE_MODE | MODE_RX_SINGLE);
  }

  return packetLength;
}

int LoRaClass::packetRssi()
{
  return (readRegister(REG_PKT_RSSI_VALUE) - (_frequency < RF_MID_BAND_THRESHOLD ? RSSI_OFFSET_LF_PORT : RSSI_OFFSET_HF_PORT));
}

float LoRaClass::packetSnr()
{
  return ((int8_t)readRegister(REG_PKT_SNR_VALUE)) * 0.25;
}
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
